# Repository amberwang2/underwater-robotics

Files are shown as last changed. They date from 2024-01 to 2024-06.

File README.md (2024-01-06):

# underwater-robotics
An underwater robot design for E96A Underwater Robotics.

<p align="center">
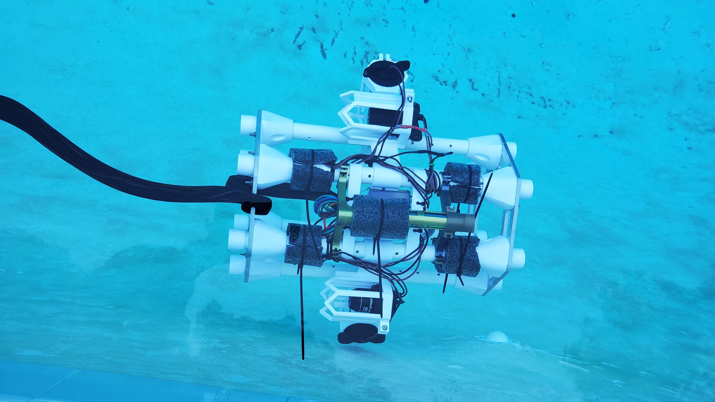
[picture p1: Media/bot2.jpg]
  
</p>

## Design Overview
The chassis consists of 2 water jetted hexagonal aluminum plates connected by 6 PVC pipes. The robot is powered by 4 bilge pump motors, which are attached using shrouds and mounts that attach to the PVC. Mounted on top of the robot is a spring-powered torpedo launcher system controlled by a servo. The chassis also includes a camera mount and an e-bay for potted wire connections from on-board components to the tether. All parts of the bot, apart from PVC pipes and aluminum plates, are designed to be either 3D printed or laser-cut out of acrylic.

On the electronics side, the controller is made up of two joysticks, an Arduino Mega, and two H-bridges to control power supply to the motors. Data from the joysticks is input to the Arduino, which converts it to the appropriate motor power and direction for each motor wired to the H-bridges. A joystick button is also wired to activate the servo controlling the torpedo launcher system.

### Flaws and additional notes
- While the aluminum plates provided stability against rolling, they also weighed it down. We were not able to make our bot neutrally buoyant and struggled to bring it back up with the motors alone. Using acrylic plates instead and adding more motors might solve this issue.
- Motor placement did not allow for going diagonally up or down since the same motors were used for left-right and up-down motion
- Moving left and right caused the bot to tilt and may have been caused by balance issues between motors or manufacturing flaws

<p align="center">
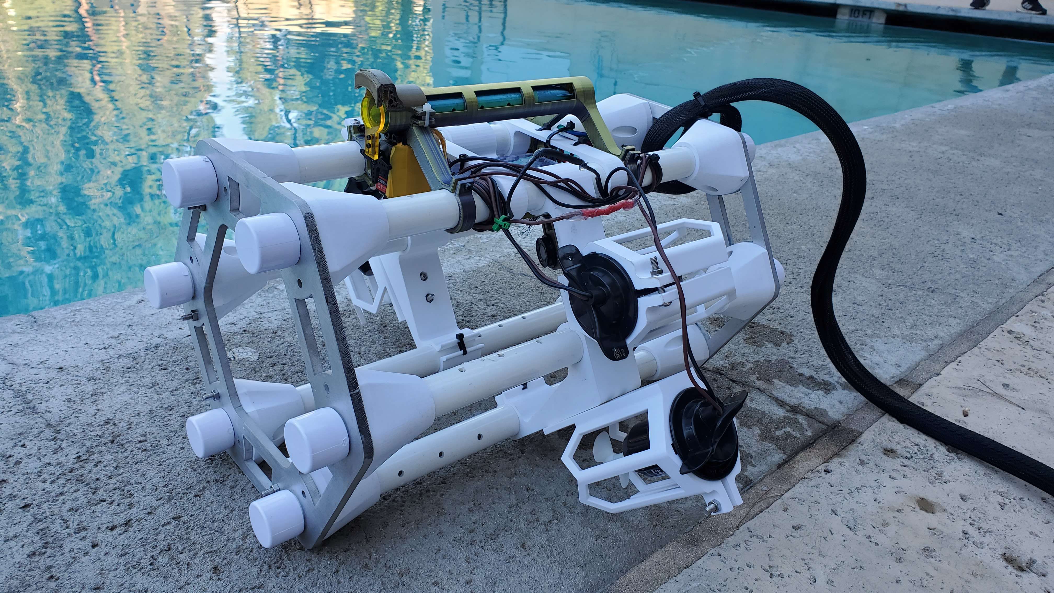
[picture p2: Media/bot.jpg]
  
</p>
<p align="center">
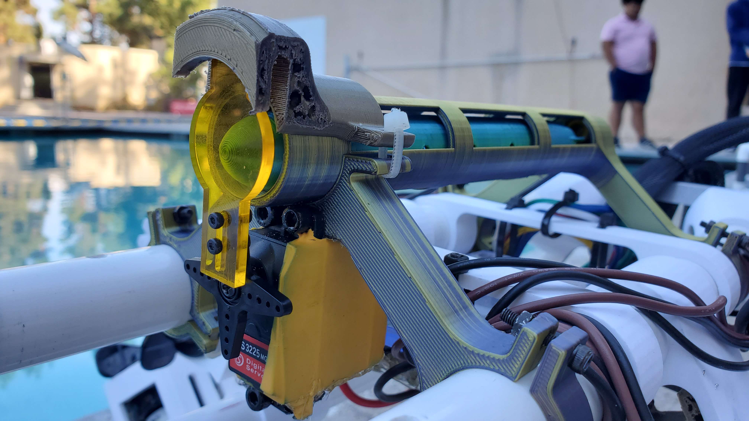
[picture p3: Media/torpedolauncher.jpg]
  
</p>
<p align="center">
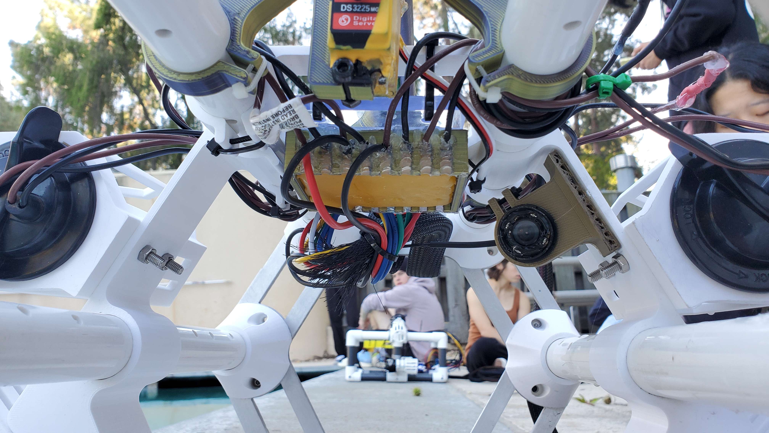
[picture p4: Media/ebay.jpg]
  
</p>
<p align="center">
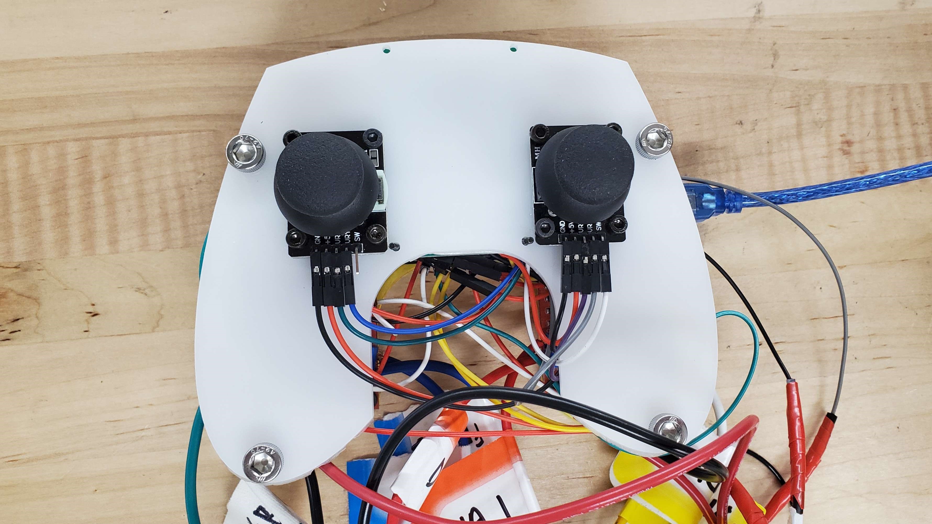
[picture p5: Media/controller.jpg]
  
&nbsp; &nbsp;
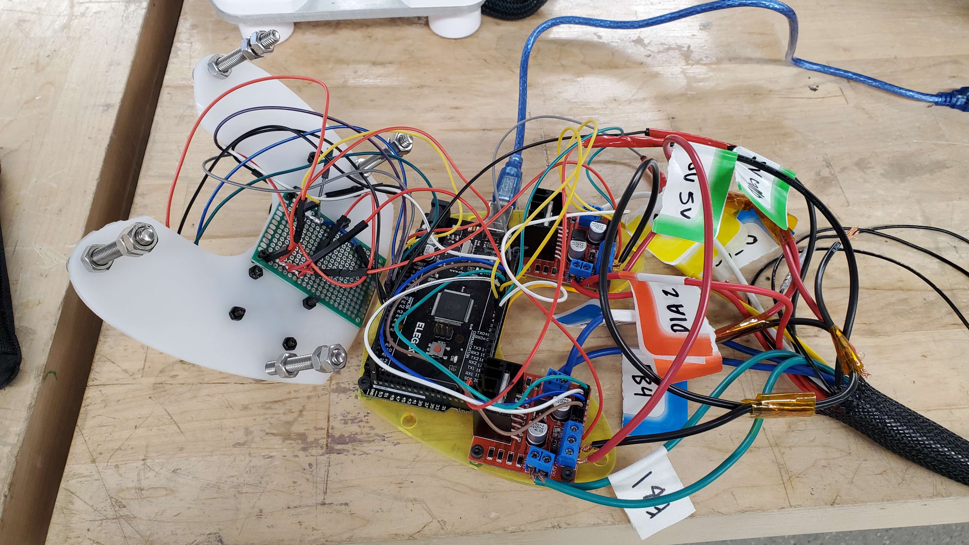
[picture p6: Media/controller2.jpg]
  
</p>
<p align="center">
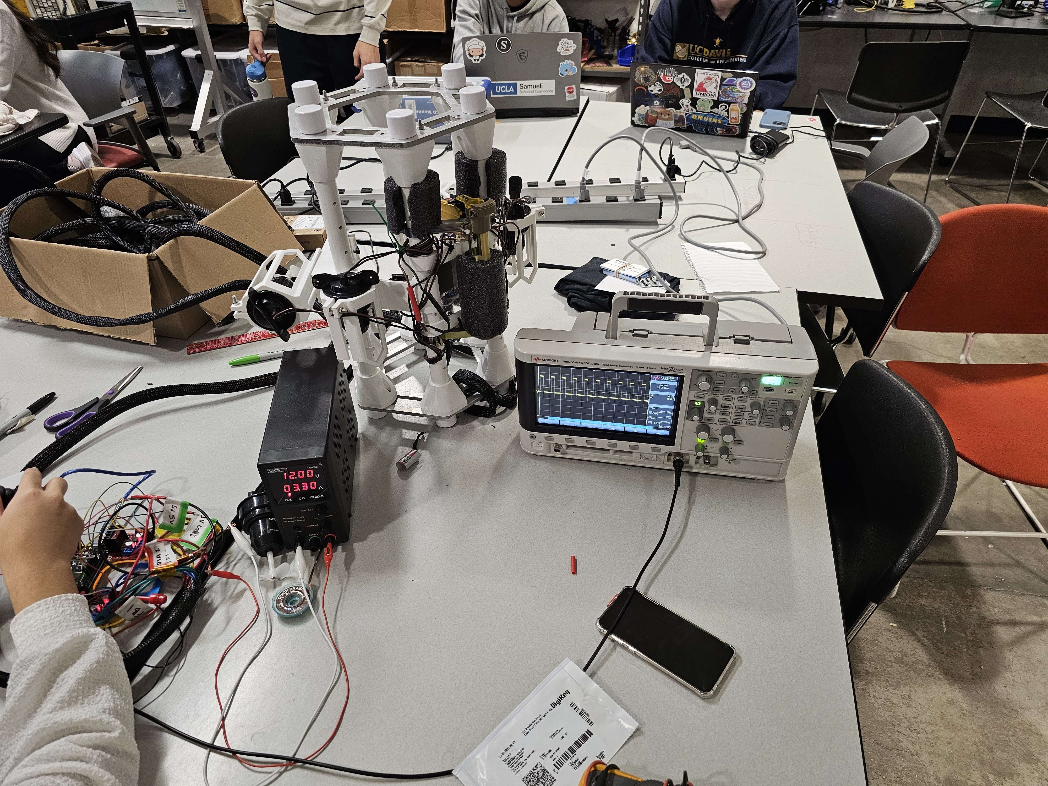
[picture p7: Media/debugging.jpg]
  
</p>
<p align="center">
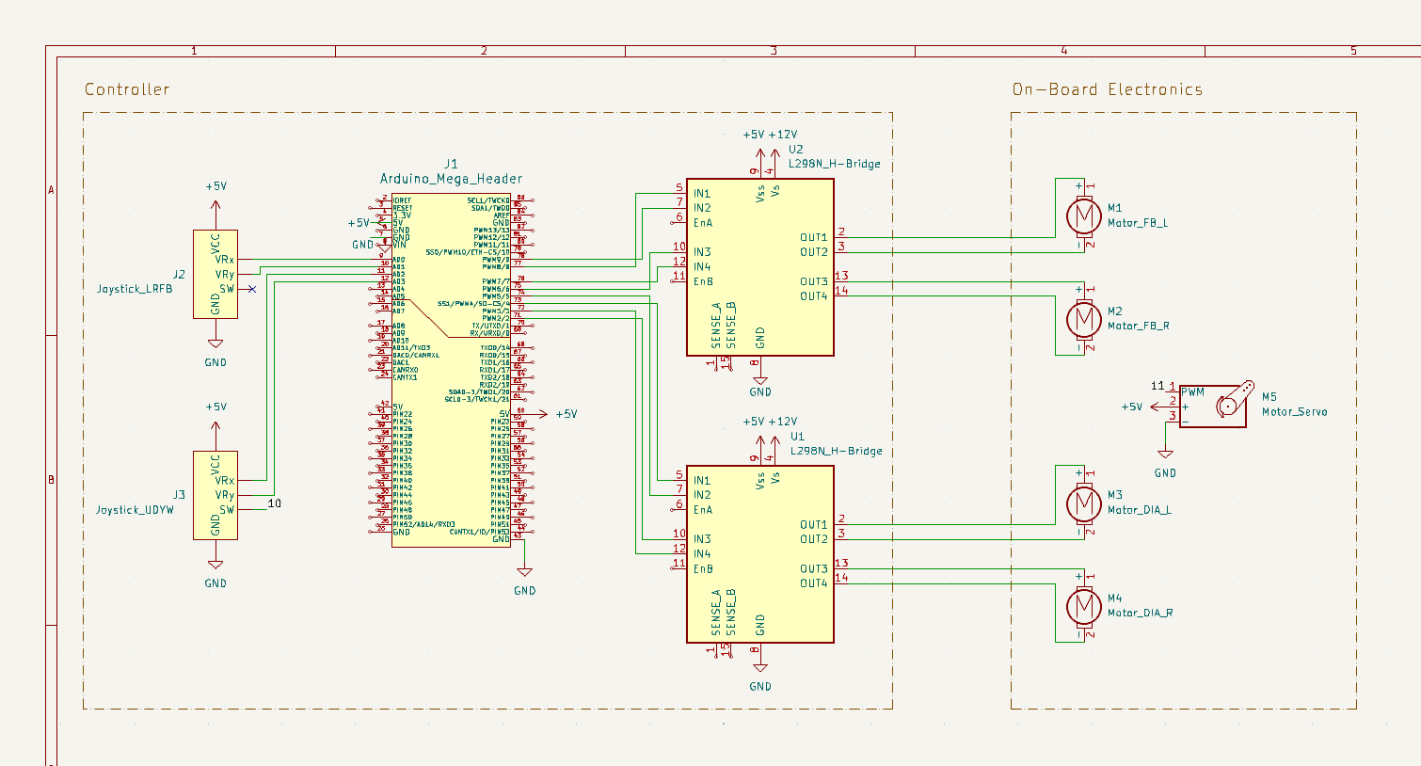
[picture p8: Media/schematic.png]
  
</p>

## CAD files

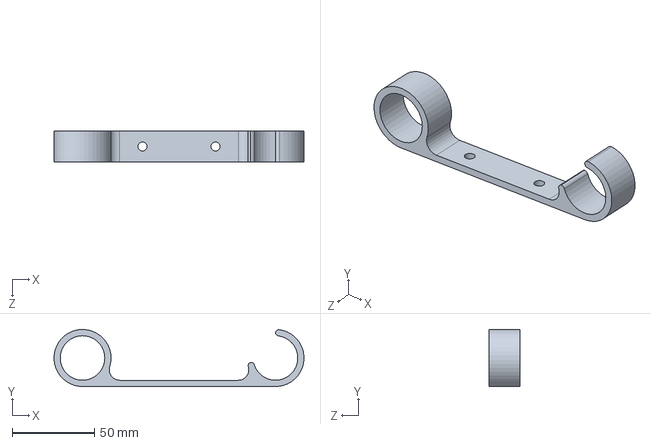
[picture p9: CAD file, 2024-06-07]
Mechanical/assembly/ebaymt.SLDPRT
152.0 x 34.7 x 19.1 mm

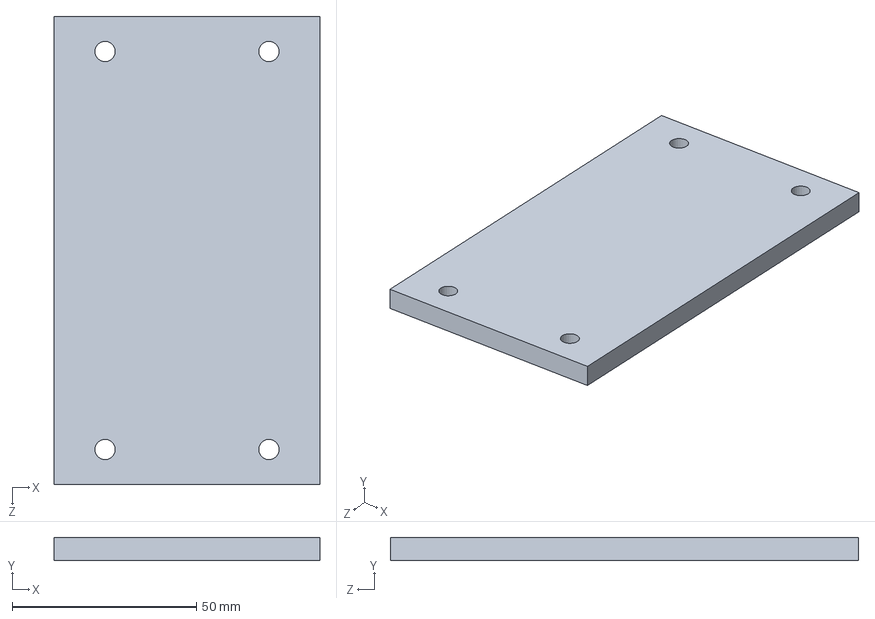
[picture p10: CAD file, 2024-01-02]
Mechanical/Chassis/ebaybase.SLDPRT
72.1 x 6.35 x 127.0 mm

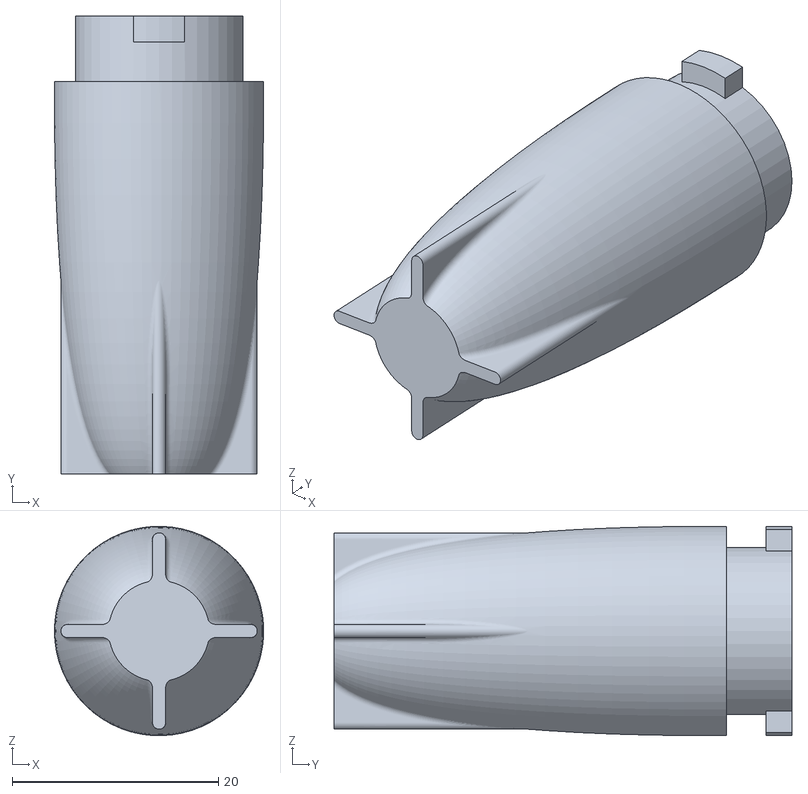
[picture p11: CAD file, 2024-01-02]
Mechanical/STL/tail.STL
20.3 x 44.5 x 20.3

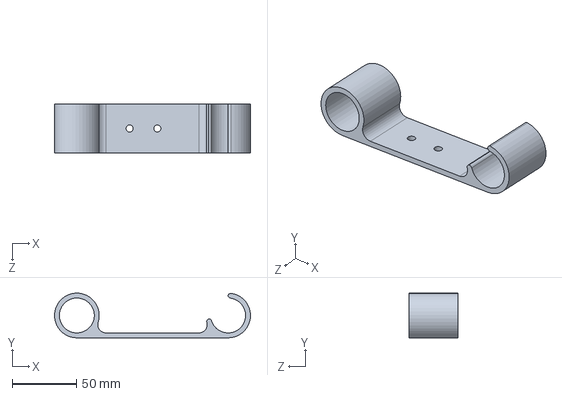
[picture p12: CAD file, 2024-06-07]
Mechanical/assembly/hmotormt.SLDPRT
152.0 x 34.7 x 38.1 mm

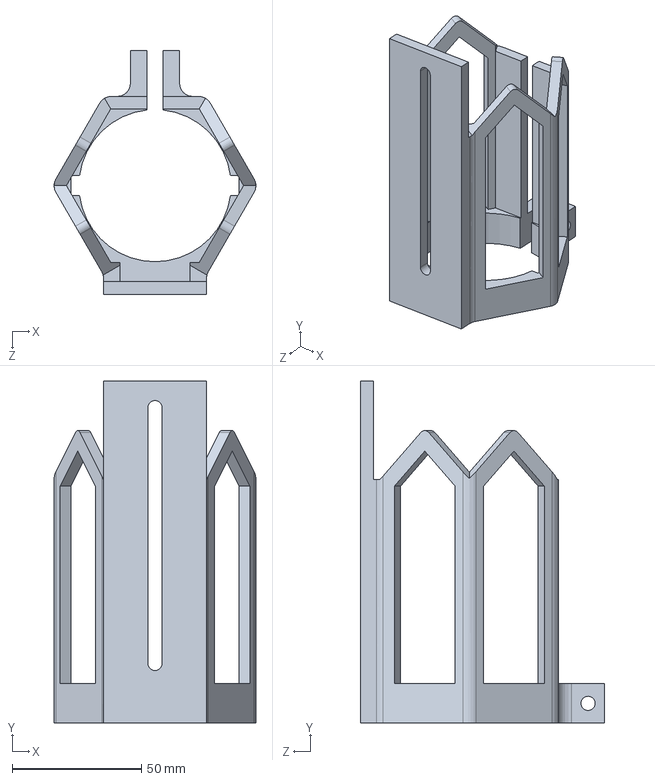
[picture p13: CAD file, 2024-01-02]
Mechanical/Chassis/motorshroud.SLDPRT
78.2 x 132.5 x 94.5 mm

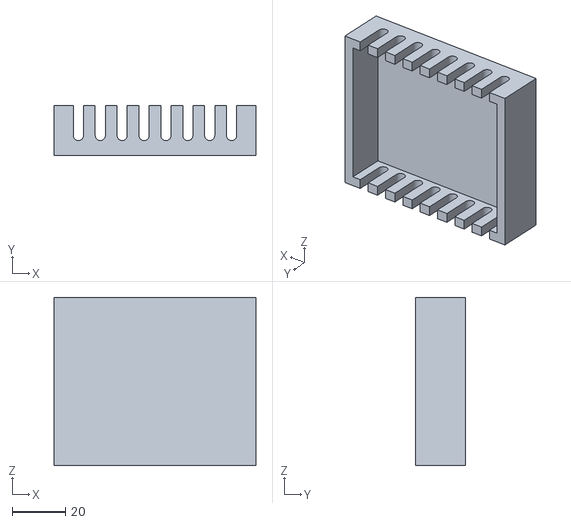
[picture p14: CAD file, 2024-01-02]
Mechanical/STL/ebay.STL
76.2 x 19.1 x 63.5

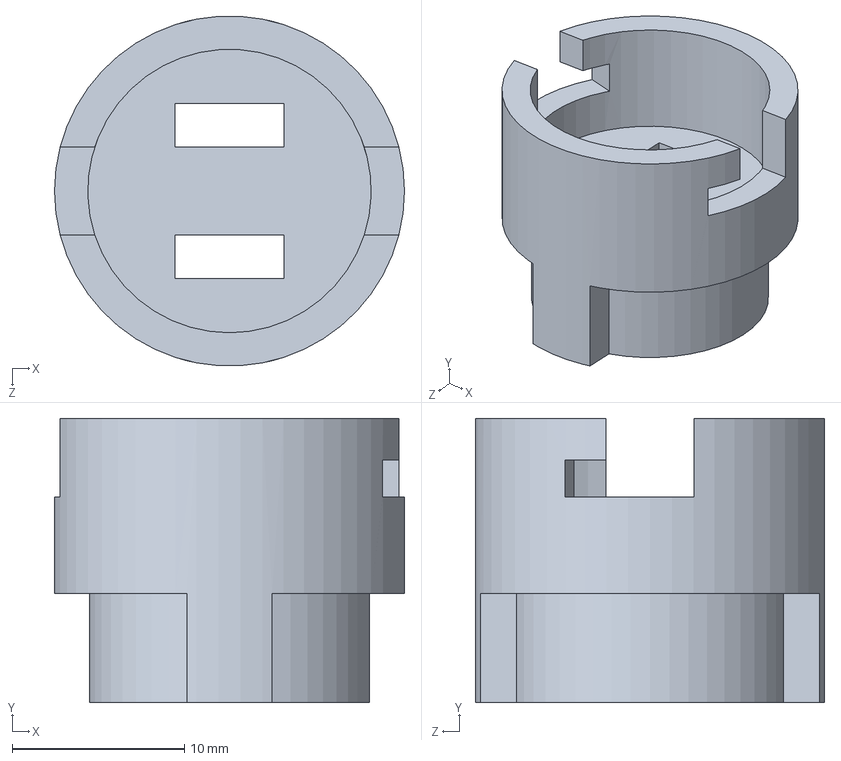
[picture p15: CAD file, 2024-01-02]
Mechanical/Torpedo/connector.SLDPRT
20.3 x 16.5 x 20.3 mm

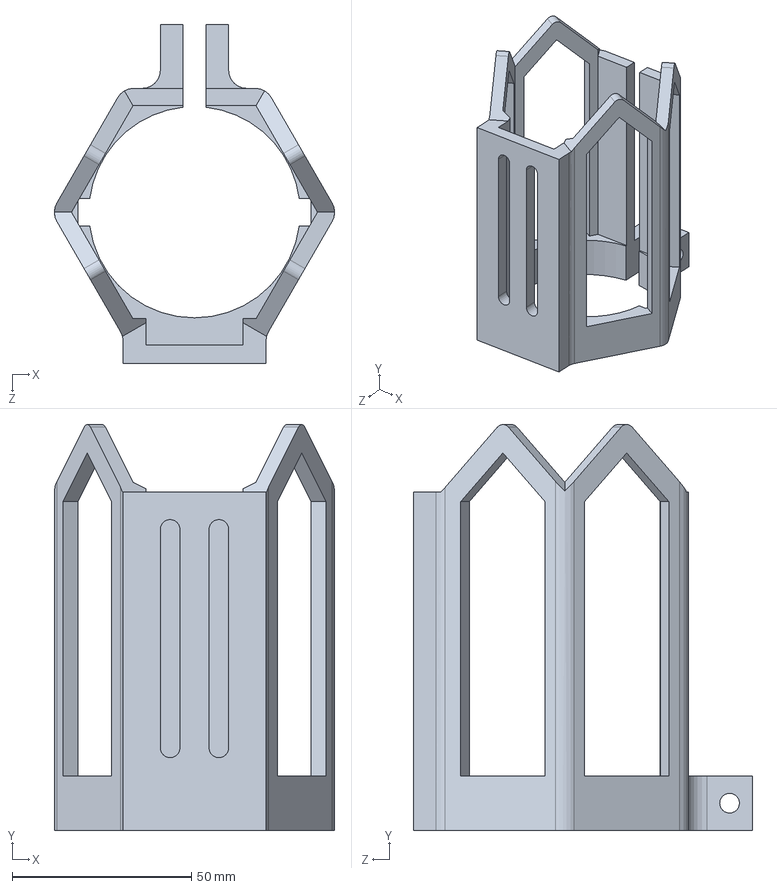
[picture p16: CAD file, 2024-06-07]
Mechanical/assembly/motorshroud.SLDPRT
78.2 x 113.2 x 94.5 mm

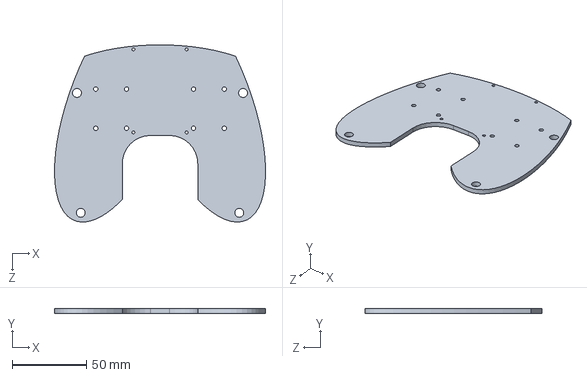
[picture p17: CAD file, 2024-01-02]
Mechanical/Chassis/controller.SLDPRT
142.0 x 3.18 x 119.2 mm

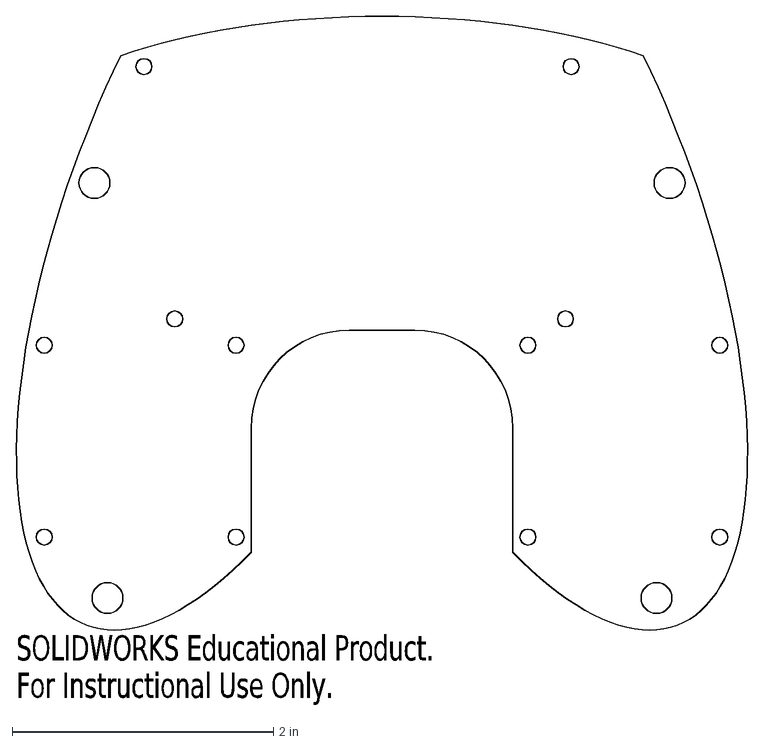
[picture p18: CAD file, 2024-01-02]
Mechanical/STL/controller_lower.DXF
SOLIDWORKS Educational Product.
For Instructional Use Only.

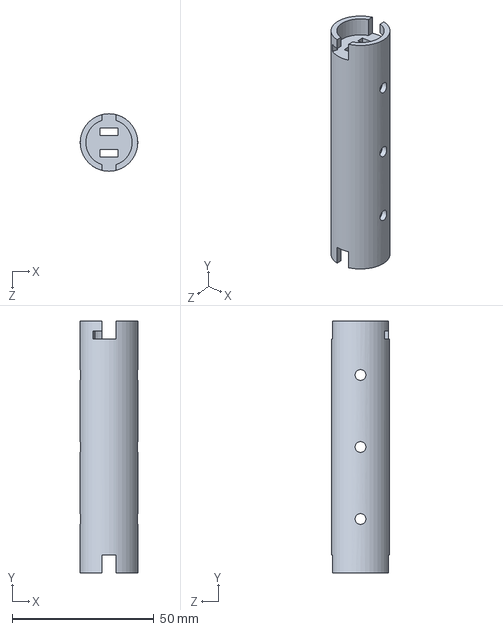
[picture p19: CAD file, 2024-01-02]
Mechanical/Torpedo/body.SLDPRT
20.3 x 88.9 x 20.3 mm

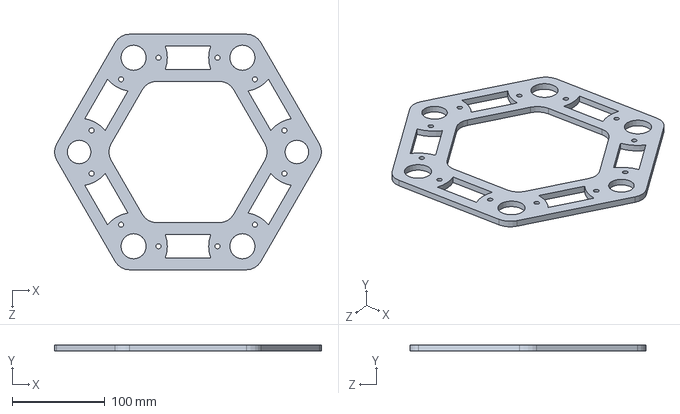
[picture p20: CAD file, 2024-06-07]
Mechanical/assembly/plate.SLDPRT
287.8 x 6.35 x 254.0 mm

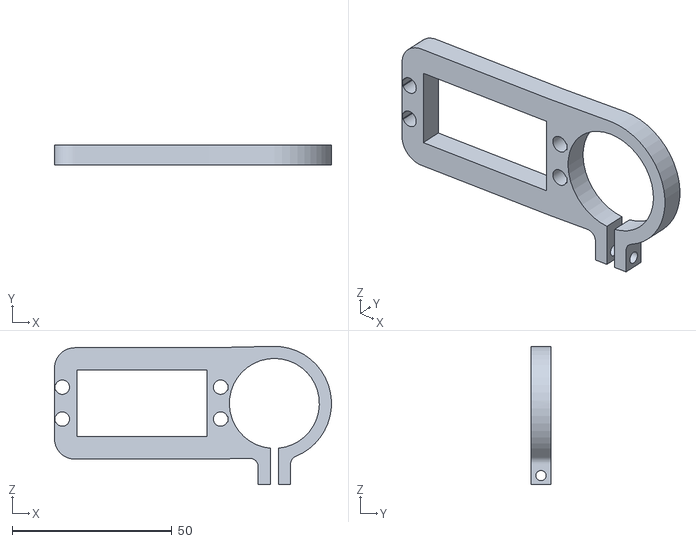
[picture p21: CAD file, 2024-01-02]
Mechanical/STL/svmount.STL
86.8 x 6.35 x 43.4

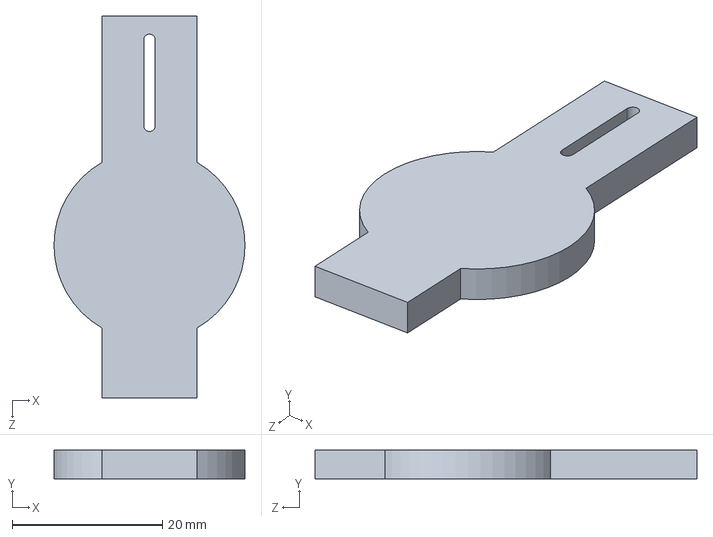
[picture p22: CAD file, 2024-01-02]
Mechanical/Torpedo/armextension.SLDPRT
25.4 x 3.81 x 50.8 mm

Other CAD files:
Mechanical/assembly/bot.SLDASM
Mechanical/Torpedo/tail.SLDPRT
Mechanical/assembly/vmotormt.SLDPRT
Mechanical/Chassis/motormt.SLDPRT
Mechanical/Chassis/91292A194_18-8 Stainless Steel Socket Head Screw.SLDPRT
Mechanical/Chassis/cameramt.SLDPRT
Mechanical/Chassis/ebay.SLDPRT
Mechanical/Chassis/plate.SLDPRT
Mechanical/STL/cameramt.STL
Mechanical/STL/connector.STL
Mechanical/STL/controller_upper.DXF
Mechanical/STL/ebaybase.DXF
Mechanical/STL/ebaymt.STL
Mechanical/STL/hmotorshroud.STL
Mechanical/STL/motormt.STL
Mechanical/STL/mount_under.STL
Mechanical/STL/nose.STL
Mechanical/STL/propeller.STL
Mechanical/STL/springplate.DXF
Mechanical/STL/tube.STL
Mechanical/STL/vmotorshroud.STL
Mechanical/Torpedo/mount.SLDPRT
Mechanical/Torpedo/nose.SLDPRT
Mechanical/Torpedo/propeller.SLDPRT
Mechanical/Torpedo/springplate.SLDPRT
Mechanical/assembly/4880K52_Standard-Wall PVC Pipe Fitting for Water.SLDPRT
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

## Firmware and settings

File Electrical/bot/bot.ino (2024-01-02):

#include <Servo.h>

Servo servo;
int LR_JS = A0;
int FB_JS = A1;
int YW_JS = A2;
int UD_JS = A3;
int SV_SW = 10;
int SV_pin = 11;
int DIA_R1 = 2;
int DIA_R2 = 3;
int DIA_L1 = 4;
int DIA_L2 = 5;
int FB_R1 = 6;
int FB_R2 = 7;
int FB_L1 = 8;
int FB_L2 = 9;
int LR_JS_value = 0;
int FB_JS_value = 0;
int YW_JS_value = 0;
int UD_JS_value = 0;
bool SV_SW_value = 0;
bool button_pressed = 0;


void setup()
{
  pinMode(DIA_R1, OUTPUT);
  pinMode(DIA_R2, OUTPUT);
  pinMode(DIA_L1, OUTPUT);
  pinMode(DIA_L2, OUTPUT);
  pinMode(FB_R1, OUTPUT);
  pinMode(FB_R2, OUTPUT);
  pinMode(FB_L1, OUTPUT);
  pinMode(FB_L2, OUTPUT);
  pinMode(LR_JS, INPUT);
  pinMode(FB_JS, INPUT);
  pinMode(YW_JS, INPUT);
  pinMode(UD_JS, INPUT);
  pinMode(SV_SW, INPUT_PULLUP);
  servo.attach(SV_pin);
  servo.write(0);
  Serial.begin(9600);
}

void loop() {
  LR_JS_value = analogRead(LR_JS);
  int LR_motor_pwr = map(abs(LR_JS_value - 511), 0, 512, 0, 255);
  FB_JS_value = analogRead(FB_JS);
  int FB_motor_pwr = map(abs(FB_JS_value - 511), 0, 512, 0, 255);
  YW_JS_value = analogRead(YW_JS);
  int YW_motor_pwr = map(abs(YW_JS_value - 511), 0, 512, 0, 255);
  UD_JS_value = analogRead(UD_JS);
  int UD_motor_pwr = map(abs(UD_JS_value - 511), 0, 512, 0, 255);
  SV_SW_value = digitalRead(SV_SW);
  Serial.println(UD_motor_pwr);
  if (LR_JS_value > 525) {
    analogWrite(DIA_R1, LR_motor_pwr);
    Serial.println("1");
    Serial.println(LR_motor_pwr);
    digitalWrite(DIA_R2, 0);
    analogWrite(DIA_L2, LR_motor_pwr);
    digitalWrite(DIA_L1, 0);
  } else if (LR_JS_value < 500) {
    analogWrite(DIA_R2, LR_motor_pwr);
    digitalWrite(DIA_R1, 0);
    analogWrite(DIA_L1, LR_motor_pwr);
    digitalWrite(DIA_L2, 0);
  } else if (UD_JS_value > 520) {
    analogWrite(DIA_R1, UD_motor_pwr);
    digitalWrite(DIA_R2, 0);
    analogWrite(DIA_L1, UD_motor_pwr);
    digitalWrite(DIA_L2, 0);
  } else if (UD_JS_value < 495) {
    analogWrite(DIA_R2, UD_motor_pwr);
    digitalWrite(DIA_R1, 0);
    analogWrite(DIA_L2, UD_motor_pwr);
    digitalWrite(DIA_L1, 0);
  } else {
    digitalWrite(DIA_R1, 0);
    digitalWrite(DIA_R2, 0);
    digitalWrite(DIA_L1, 0);
    digitalWrite(DIA_L2, 0);
  }
  if (FB_JS_value > 535) {
    analogWrite(FB_R1, FB_motor_pwr);
    digitalWrite(FB_R2, 0);
    analogWrite(FB_L1, FB_motor_pwr);
    digitalWrite(FB_L2, 0);
  } else if (FB_JS_value < 510) {
    analogWrite(FB_R2, FB_motor_pwr);
    digitalWrite(FB_R1, 0);
    analogWrite(FB_L2, FB_motor_pwr);
    digitalWrite(FB_L1, 0);
  } else if (YW_JS_value > 515) {
    analogWrite(FB_R2, YW_motor_pwr);
    digitalWrite(FB_R1, 0);
    analogWrite(FB_L1, YW_motor_pwr);
    digitalWrite(FB_L2, 0);
  } else if (YW_JS_value < 490) {
    analogWrite(FB_R1, YW_motor_pwr);
    digitalWrite(FB_R2, 0);
    analogWrite(FB_L2, YW_motor_pwr);
    digitalWrite(FB_L1, 0);
  } else {
    digitalWrite(FB_R1, 0);
    digitalWrite(FB_R2, 0);
    digitalWrite(FB_L1, 0);
    digitalWrite(FB_L2, 0);
  }
  if (!button_pressed) {
    if (!SV_SW_value) {
      // activate servo
      servo.write(45);
      button_pressed = 1;
    }
  }


  
  delay(100);
  
}

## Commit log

2024-01-02 File organization
    [4880K52_Standard-Wall PVC Pipe Fitting for Water.SLDPRT, 91292A192_18-8 Stainless Steel Socket Head Screw.SLDPRT, 91292A194_18-8 Stainless Steel Socket Head Sc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]
2024-01-02 Rename assembly.zip
2024-01-03 Add schematic
    [schematic.kicad_pcb, schematic.kicad_sch]
2024-01-03 Rename electrical folder
    [schematic.kicad_pcb, schematic.kicad_sch]
2024-01-03 Add schematic.png
2024-06-07 update assembly
    [4880K52_Standard-Wall PVC Pipe Fitting for Water.SLDPRT, 91292A192_18-8 Stainless Steel Socket Head Screw.SLDPRT, 91828A241_18-8 Stainless Steel Hex Nut.SLDPRT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]
